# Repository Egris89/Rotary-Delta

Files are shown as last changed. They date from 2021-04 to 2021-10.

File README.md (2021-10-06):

Rotary Delta,

inspired by the Icepick Delta Project this is my latest Version of a Rotary Delta. Most of the Parts are printed. You need a workspace of 300x300mm to be able to print all Parts.

I used PETG as material and an infill-ratio of 50% with 4 Perimeters and 4 Top & Bottom Layers. You should be familiar in using manuel placed supports. I oriented the STL files as I printed them. I recommend to alaign your Printer as good as possible in X/Y/Z orientation because this will have an effect to the accuracy of the machine.

-------------------------------------------------------------------------------------------------------------------------
You will need following Parts for the assambly:

-> Bearing 608ZZ  18x

-> Bearing 696ZZ  18x

-> Shaft, Diameter 6mm, length 52mm    6x

-> Shaft, Diameter 8mm, length 82mm    3x

-> Shaft, Diameter 8mm, lenght 145mm   3x

-> Hexagonal Spacers, lenght 20mm, M4

-> Carbon Rod, Diameter 30mm, Inner Diameter 28mm, lenght 173mm, 3 pieces

-> Carbon Rod, Diameter 8mm, lenght 375mm, 6 pieces

-> 11mm Steel Balls with M4 Threads

-> Opto Endstops

-> Super-Glue

-> Nema 17

-> HTD 3M 9mm Pulley, 40 teeth  3x

-> HTD 3M 9mm Pulley, 20 teeth 3x

-> HTD 3M 9mm Pulley, 14 teeth 3x

-> HTD 3M 9mm Belts,

-> HTD 3M closed belt with 174mm 58 theeth, 3x

-> Aluminium-Shaft, Diameter 28mm, Lenght 122mm, M5 Threads on Bottom & Top

-------------------------------------------------------------------------------------------------------------------------------------------------
Some Values for FW-Setup:

Base-Radius: 80mm

Effector-Radius: 35mm

Arm-Lenght: 190mm

Rod-Lenght: 394mm

Angle when homed: about 46.50°  (When you measure the arm-angle on bottom of the Carbon-Rod you have to substract 7.9° to get the correct angle)

Stepps per deg with x32 Micro-Stepping and 1.8° Stepper: 391

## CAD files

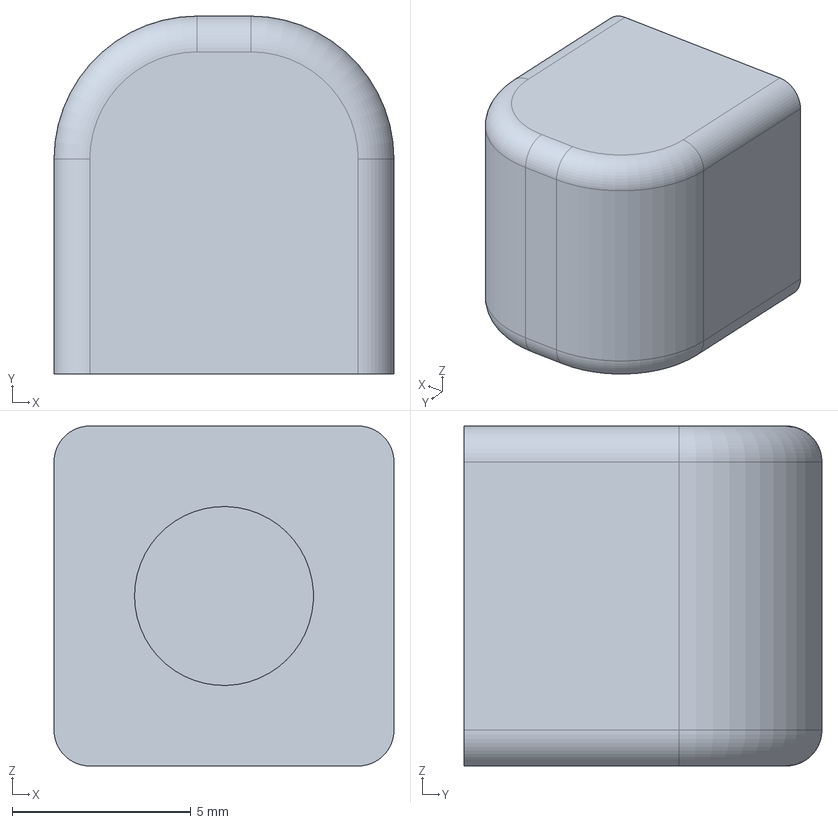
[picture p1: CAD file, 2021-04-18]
STEP/Arm/Belt_Tension.step
9.50 x 10.0 x 9.50 mm

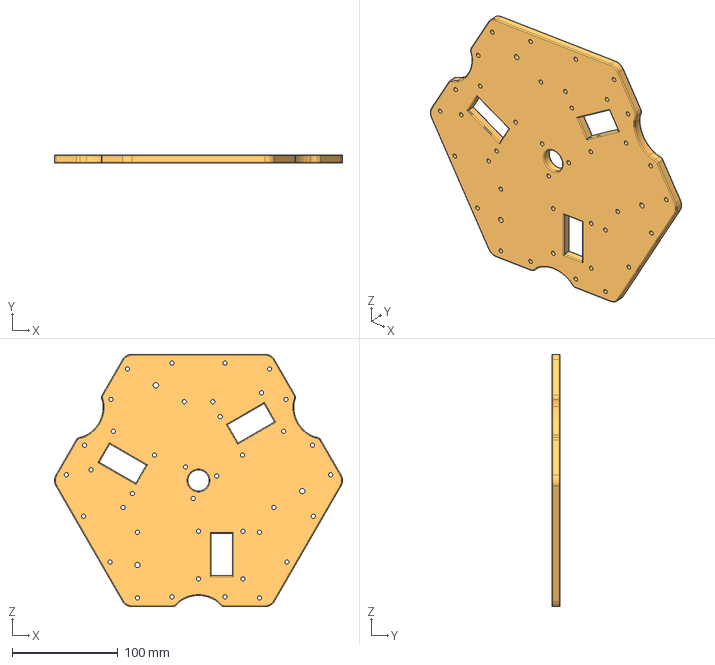
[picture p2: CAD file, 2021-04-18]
STEP/Base/Bottom_Plate.step
272.3 x 8.00 x 238.5 mm

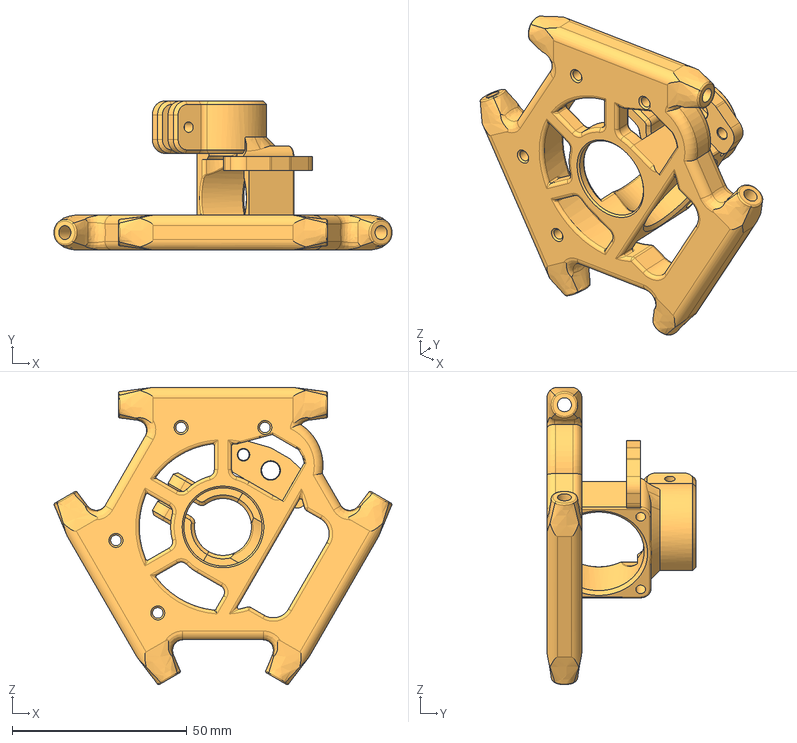
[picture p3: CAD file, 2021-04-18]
STEP/Effector/Effector_FDM.step
96.8 x 42.7 x 85.2 mm

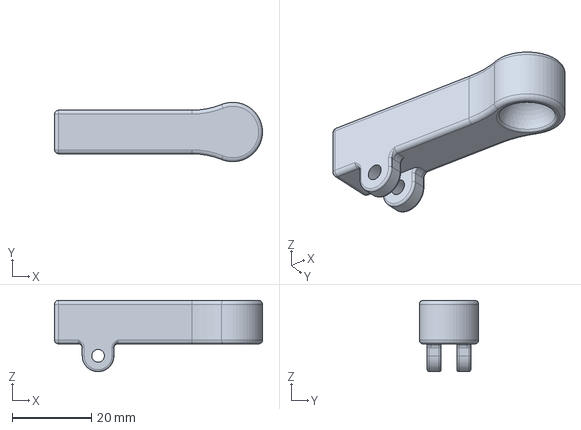
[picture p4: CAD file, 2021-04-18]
STEP/Rod/Rod_Joint.step
52.5 x 15.0 x 18.0 mm

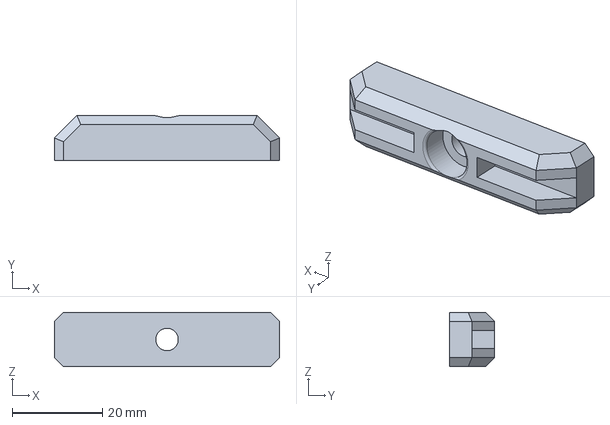
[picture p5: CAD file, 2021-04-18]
STEP/Arm/Belt_Clamp.step
50.0 x 10.0 x 12.0 mm

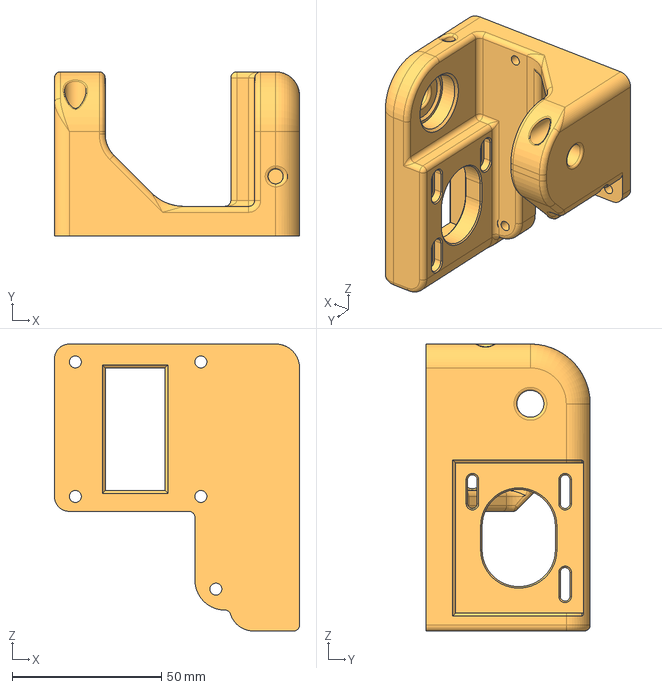
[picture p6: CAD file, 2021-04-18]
STEP/Base/Motor_Mount.step
82.0 x 55.0 x 96.0 mm

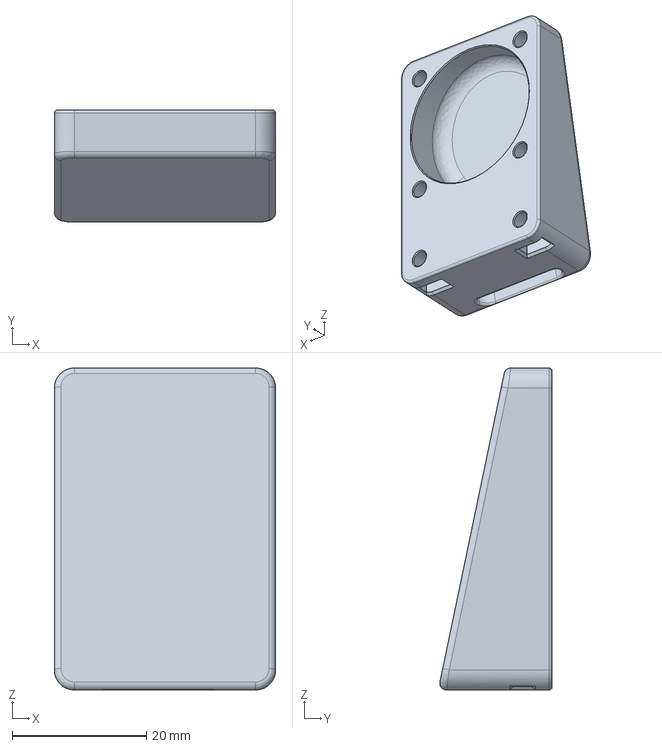
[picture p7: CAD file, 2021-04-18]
STEP/Effector/Filament_Cooling.step
33.0 x 16.8 x 48.0 mm

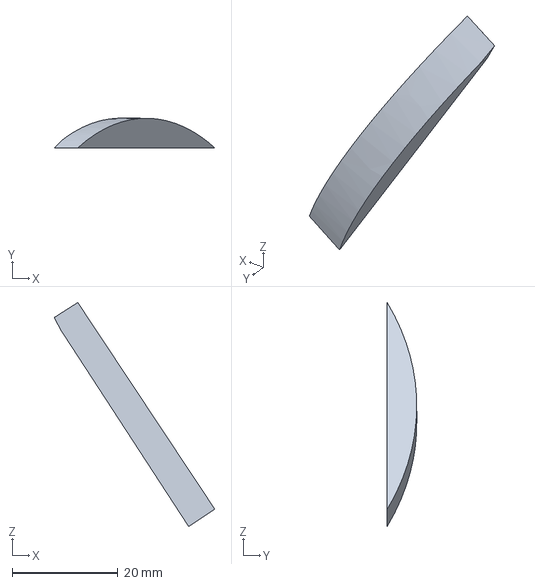
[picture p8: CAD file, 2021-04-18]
STEP/Arm/Wheel_Reinf.step
30.4 x 5.62 x 42.4 mm

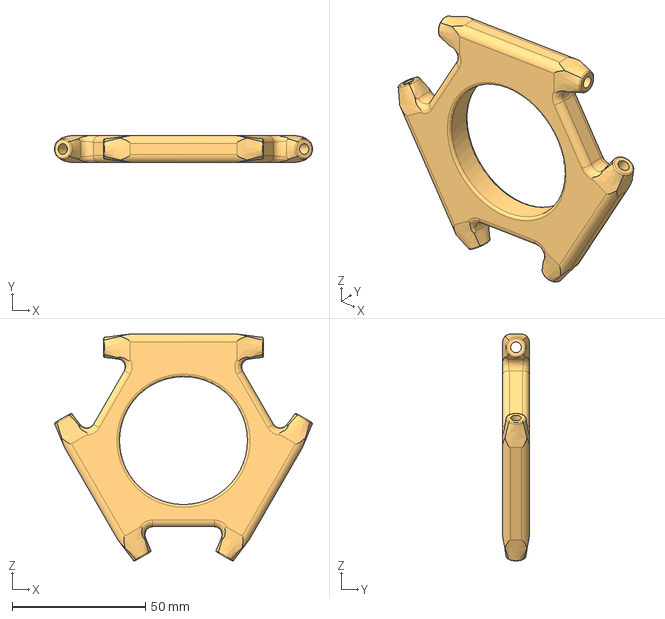
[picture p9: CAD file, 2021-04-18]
STEP/Effector/Effector_Base.step
96.8 x 10.0 x 85.2 mm

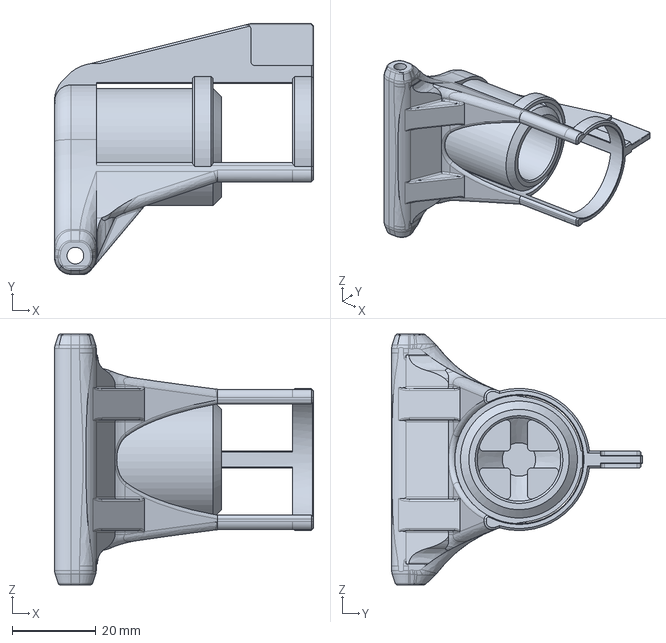
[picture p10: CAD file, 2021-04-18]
STEP/Arm/Arm_Finger.step
62.0 x 60.0 x 60.0 mm

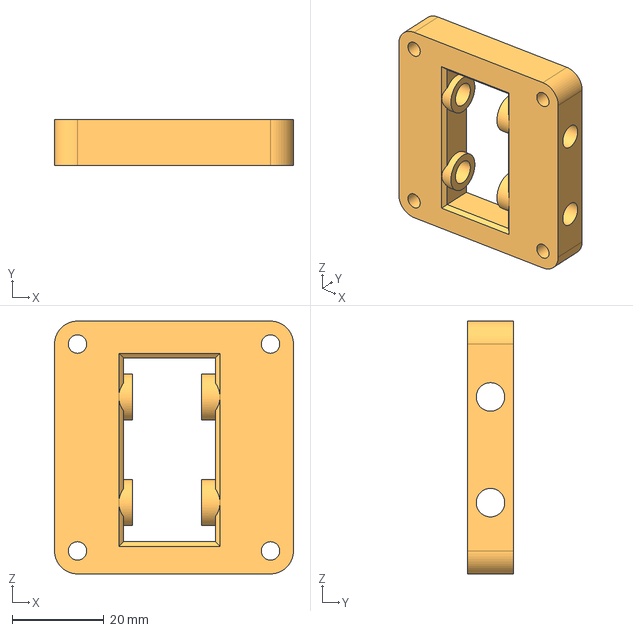
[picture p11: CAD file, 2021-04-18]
STEP/Base/Belt_Diversion.step
52.0 x 10.0 x 55.0 mm

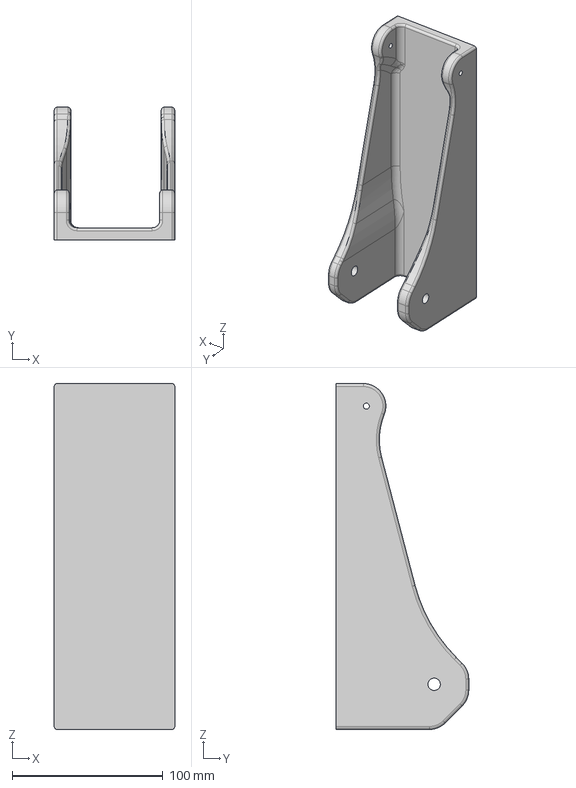
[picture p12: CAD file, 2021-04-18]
STEP/Arm/Arm_Mounting_Device.step
80.0 x 88.0 x 229.6 mm

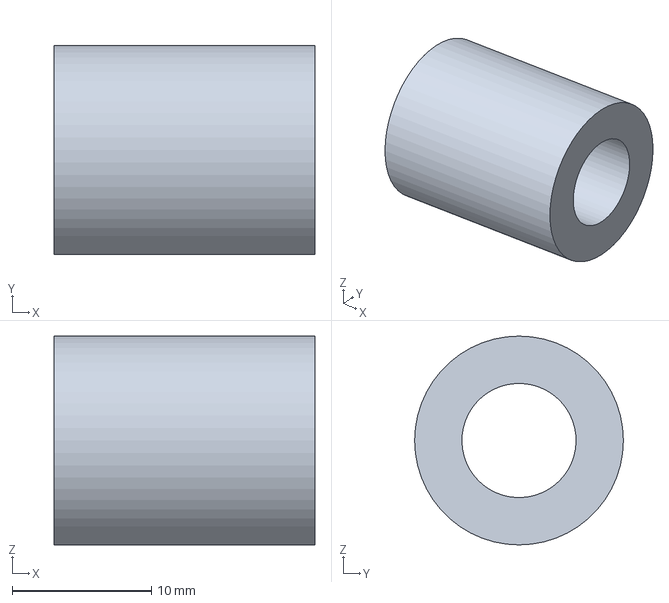
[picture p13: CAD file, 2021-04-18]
STEP/Base/Spacer_Arm_Left.step
18.8 x 15.0 x 15.0 mm

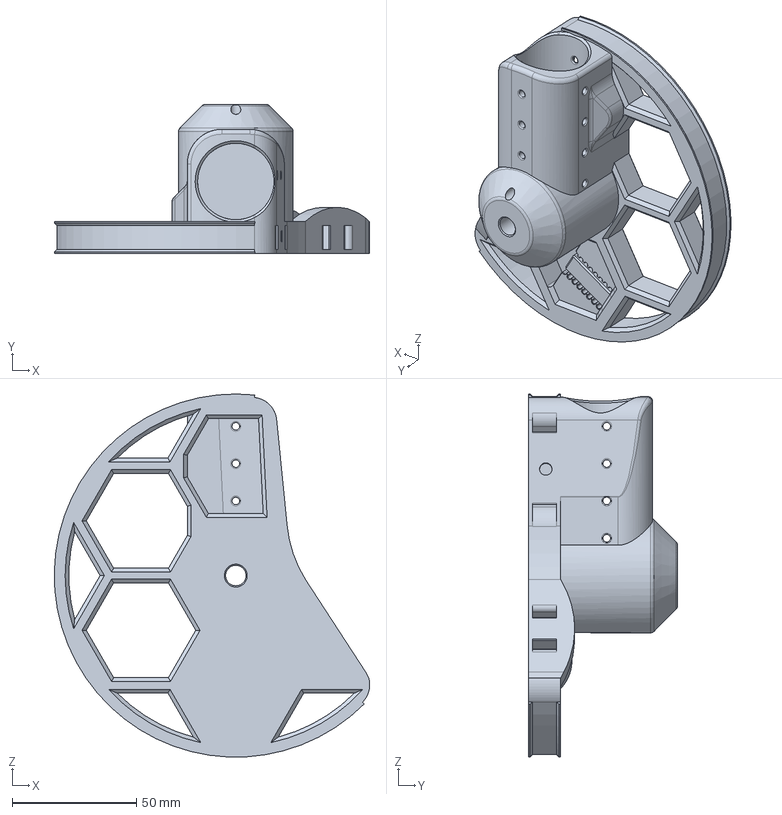
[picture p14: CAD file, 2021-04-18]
STEP/Arm/Wheel_experimental.step
126.8 x 60.0 x 145.9 mm

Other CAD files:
STEP/Base/Top_Plate.step
STEP/Base/Spacer_Pulley.step
STEP/Arm/Wheel.step
STEP/Base/Arm_Intake.step
STEP/Base/Base_Reinf.step
STEP/Base/Endstop_Mount.step
STEP/Base/Spacer_Arm_Right.step
STL/Arm/Arm_Finger.stl
STL/Arm/Arm_Mounting_Device.stl
STL/Arm/Belt_Clamp.stl
STL/Arm/Belt_Tension.stl
STL/Arm/Wheel.stl
STL/Arm/Wheel_Reinf.stl
STL/Arm/Wheel_experimental.stl
STL/Base/Arm_Intake.stl
STL/Base/Base_Reinf.stl
STL/Base/Belt_Diversion.stl
STL/Base/Bottom_Plate.stl
STL/Base/Endstop_Mount.stl
STL/Base/Motor_Mount.stl
STL/Base/Spacer_Arm_Left.stl
STL/Base/Spacer_Arm_Right.stl
STL/Base/Spacer_Pulley.stl
STL/Base/Top_Plate.stl
STL/Effector/Effector_Base.stl
STL/Effector/Effector_FDM.stl
STL/Effector/Filament_Cooling.stl
STL/Rod/Rod_Joint.stl

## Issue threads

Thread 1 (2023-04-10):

more testing requested, developing a larger scale delta robot based on your design

manu7irl, 2023-04-10:
Could you please contact me, we talked on discord a few months ago.
I want to redesign your project to fit a larger print volume, I have your step files but the assembly should be better to understand what is what and where to fit everything, also I would like to make it more parametric to create a frame according to the print volume selected. I already made a tool with chatgpt that helped me alot to go that way but your help will be greatly appreciated!
Thanks for contacting me,
Emanuel Sharvit
manu7irl@gmail.com

LBalera, 2024-08-14:
I would like collaborate to this project. If you still working on it, please contact me too.

luis.balera@live.com

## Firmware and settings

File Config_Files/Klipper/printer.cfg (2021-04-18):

# This file contains common pin mappings for Duet2 Eth/Wifi boards. To
# use this config, the firmware should be compiled for the SAM4E8E.

# See docs/Config_Reference.md for a description of parameters.

[gcode_macro Accept_CMD]
gcode:
    ACCEPT

[gcode_macro SAVE_CMD]
gcode:
    SAVE_CONFIG

[gcode_macro ABORT_CMD]
gcode:
    ABORT

[gcode_macro Calibrate_Probe]
gcode:
    PROBE_CALIBRATE
    
[gcode_macro Calibrate_Printer]
gcode:
    DELTA_CALIBRATE

[gcode_macro Calibrate_Printer_ManMode]
gcode:
   DELTA_CALIBRATE METHOD=manual

[gcode_macro Calibrate_Bed]
gcode:
    BED_MESH_CALIBRATE
    
[gcode_macro Load_Bedmesh]
gcode:
    BED_MESH_PROFILE LOAD=default

[virtual_sdcard]
path: ~/gcode_files

[pause_resume]

[display_status]

[gcode_macro CANCEL_PRINT]
rename_existing: BASE_CANCEL_PRINT
gcode:
    TURN_OFF_HEATERS
    CLEAR_PAUSE
    SDCARD_RESET_FILE
    BASE_CANCEL_PRINT

[gcode_macro PAUSE]
rename_existing: BASE_PAUSE
# change this if you need more or less extrusion
variable_extrude: 1.0
gcode:
    ##### read E from pause macro #####
    {% set E = printer["gcode_macro PAUSE"].extrude|float %}
    ##### set park positon for x and y #####
    # default is your max posion from your printer.cfg
    {% set x_park = printer.toolhead.axis_maximum.x|float - 5.0 %}
    {% set y_park = printer.toolhead.axis_maximum.y|float - 5.0 %}
    ##### calculate save lift position #####
    {% set max_z = printer.toolhead.axis_maximum.z|float %}
    {% set act_z = printer.toolhead.position.z|float %}
    {% if act_z < (max_z - 2.0) %}
        {% set z_safe = 2.0 %}
    {% else %}
        {% set z_safe = max_z - act_z %}
    {% endif %}
    ##### end of definitions #####
    SAVE_GCODE_STATE NAME=PAUSE_state
    BASE_PAUSE
    G91
    G1 E-{E} F2100
    G1 Z{z_safe} F900
    G90
    G1 X{x_park} Y{y_park} F6000
  
[gcode_macro RESUME]
rename_existing: BASE_RESUME
gcode:
    ##### read E from pause macro #####
    {% set E = printer["gcode_macro PAUSE"].extrude|float %}
    ##### end of definitions #####
    G91
    G1 E{E} F2100
    RESTORE_GCODE_STATE NAME=PAUSE_state
    BASE_RESUME


# This file is an example config file for rotary delta style printers.
# One may copy and edit this file to configure a new delta printer.

# ROTARY DELTA KINEMATICS ARE A WORK IN PROGRESS. Homing moves may
# timeout and some boundary checks are not implemented.

# See docs/Config_Reference.md for a description of parameters.

[stepper_a]
step_pin: PD6
dir_pin: PD11
enable_pin: !PC6
full_steps_per_rotation: 200
microsteps: 128
gear_ratio: 21.88125:1
endstop_pin: ^PC14
homing_speed: 20
upper_arm_length: 190.000
lower_arm_length: 393.00
angle: 270.00
position_endstop: 197.5

[tmc2660 stepper_a]
cs_pin: PD14
spi_bus: usart1
run_current: 1.000
sense_resistor: 0.051

[stepper_b]
step_pin: PD7
dir_pin: PD12
enable_pin: !PC6
full_steps_per_rotation: 200
microsteps: 128
gear_ratio: 21.88125:1
endstop_pin: ^PA2
homing_speed: 20
upper_arm_length: 190.000
lower_arm_length: 393.00
angle: 30.00
position_endstop: 197.5

[tmc2660 stepper_b]
cs_pin: PC9
spi_bus: usart1
run_current: 1.000
sense_resistor: 0.051

[stepper_c]
step_pin: PD8
dir_pin: !PD13
enable_pin: !PC6
full_steps_per_rotation: 200
microsteps: 128
gear_ratio: 21.88125:1
endstop_pin: ^PD29
homing_speed: 20
upper_arm_length: 190.000
lower_arm_length: 393.00
angle: 150.00
position_endstop: 197.2

[tmc2660 stepper_c]
cs_pin: PC10
spi_bus: usart1
run_current: 1.000
sense_resistor: 0.051

[extruder]
step_pin: PD5
dir_pin: !PA1
enable_pin: !PC6
full_steps_per_rotation: 400
microsteps: 32
rotation_distance: 7.646
nozzle_diameter: 0.400
filament_diameter: 1.750
heater_pin: !PA20
sensor_type: EPCOS 100K B57560G104F
sensor_pin: PC15
control: pid
#pid_Kp: 22.2
#pid_Ki: 1.08
#pid_Kd: 114
min_temp: 0
max_temp: 300

[tmc2660 extruder]
cs_pin: PC17
spi_bus: usart1
run_current: 1.000
sense_resistor: 0.051

[heater_bed]
heater_pin: !PA19
sensor_type: EPCOS 100K B57560G104F
sensor_pin: PC13
#control: pid
#pid_Kp: 54.027
#pid_Ki: 0.770
#pid_Kd: 948.182
min_temp: 0
max_temp: 130

[mcu]
serial: /dev/serial/by-id/usb-Klipper_sam4e8e_0031375359544E573134303536303039-if00

[fan]
pin: PC23  # FAN0

[bltouch]
sensor_pin: ^PC16
control_pin: PA15
pin_move_time: 0.080
stow_on_each_sample: True
probe_with_touch_mode: False
pin_up_reports_not_triggered: True
pin_up_touch_mode_reports_triggered: True
x_offset: -20.7
y_offset: -3.8
z_offset: 3.521
speed: 25.0
samples: 6
sample_retract_dist: 10
samples_result: average
samples_tolerance: 0.050
samples_tolerance_retries: 2
lift_speed: 100

[bed_mesh]
speed: 120
horizontal_move_z: 10
mesh_min: -140,-140
mesh_max: 140,140
probe_count: 4,4
mesh_pps: 6,6
algorithm: bicubic
bicubic_tension: 0.2

[input_shaper]
shaper_freq_x: 25
shaper_freq_y: 25
shaper_type: ei

[printer]
kinematics: rotary_delta
max_velocity: 300
max_accel: 3000
max_z_velocity: 300
minimum_z_position: -5
shoulder_radius: 45
shoulder_height: 411.45


[delta_calibrate]
radius: 50
speed: 50
horizontal_move_z: 10

#*# <---------------------- SAVE_CONFIG ---------------------->
#*# DO NOT EDIT THIS BLOCK OR BELOW. The contents are auto-generated.
#*#
#*# [heater_bed]
#*# control = pid
#*# pid_kp = 56.922
#*# pid_ki = 2.259
#*# pid_kd = 358.609
#*#
#*# [extruder]
#*# pid_kp = 23.331
#*# pid_ki = 1.265
#*# pid_kd = 107.616
#*#
#*# [bed_mesh default]
#*# version = 1
#*# points =
#*# 	  0.109155, -0.101273, -0.154432, -0.241082
#*# 	  0.324392, 0.165513, -0.041063, -0.269132
#*# 	  0.395090, 0.184716, 0.072583, -0.066008
#*# 	  0.429470, 0.280607, 0.194680, 0.038100
#*# tension = 0.2
#*# min_x = -140.01
#*# algo = bicubic
#*# y_count = 4
#*# mesh_y_pps = 6
#*# min_y = -140.0
#*# x_count = 4
#*# max_y = 139.99
#*# mesh_x_pps = 6
#*# max_x = 139.99
